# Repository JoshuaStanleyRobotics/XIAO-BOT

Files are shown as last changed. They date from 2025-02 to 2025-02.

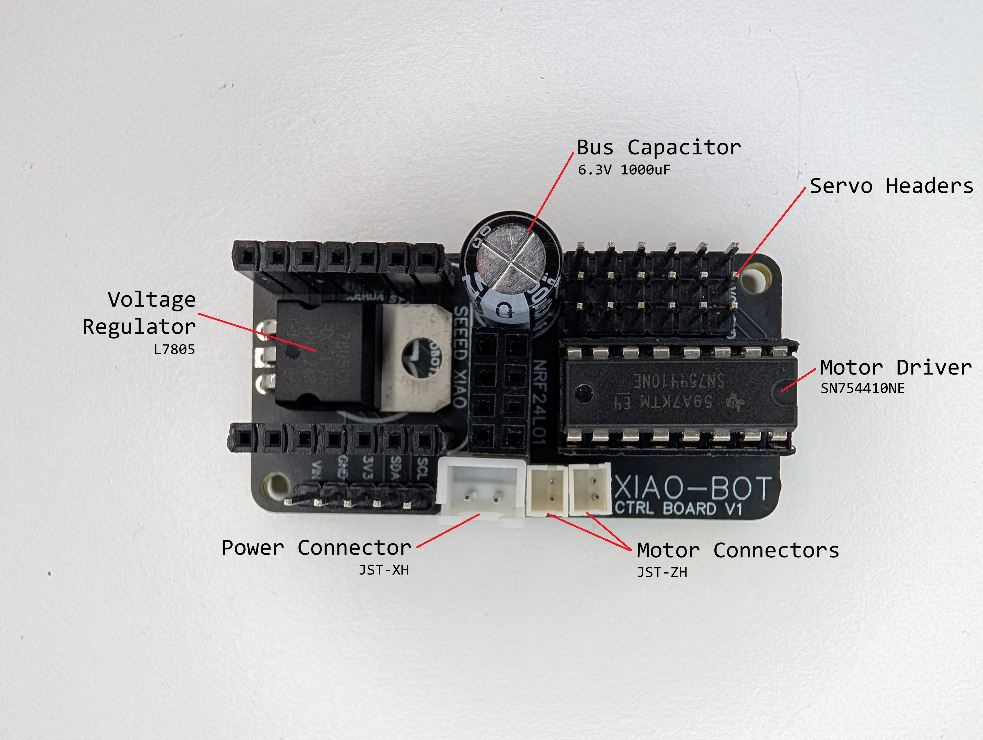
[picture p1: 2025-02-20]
Control Board/Images/04_Optional Components.jpg

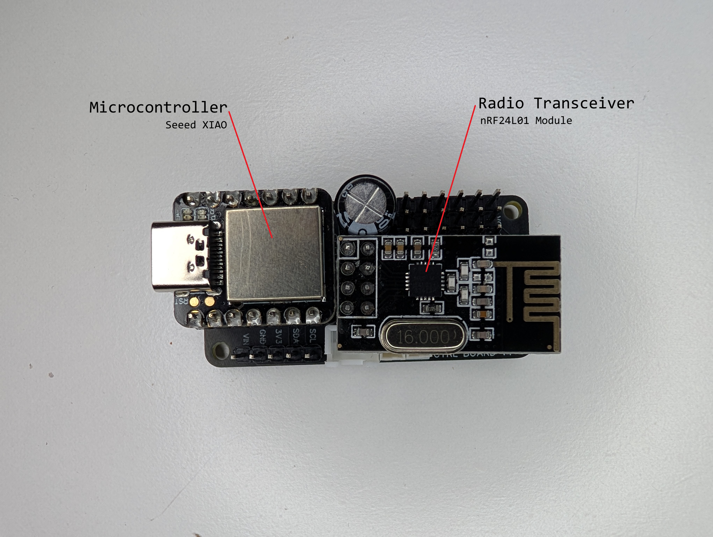
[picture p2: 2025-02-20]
Control Board/Images/03_Required Components.jpg

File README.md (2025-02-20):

# XIAO-BOT

## Control Board


The Control Board interfaces the microcontroller (a Seeed XIAO board) with a radio transceiver (nRF24L01 module) to act as the base of a compact, remote control robotics platform.
  The nRF24L01 board is wired to the standard SPI pins on the XIAO with the CE and CSN pins wired to D6 and D7 respectively. For a compatible remote check out https://github.com/JoshuaStanleyRobotics/Robot-Remote
	
Breakout servo headers are included wired to pins D0-D5 to allow for controlling up to 6 servo motors at once. 
	On the bottom side of the board, there are solder pads to select the supply voltage (VCC) for the servo headers and motor driver.
		Solder the corresponding pad to the center pad to select either the voltage supplied to the board (VIN) or the regulated voltage (5V).
	Space for an optional bus capacitor is included to help smooth the 5V supply voltage. 

A second set of breakout pins include power and I2C connections for expansions boards.
  Note: I2C uses pins D4 and D5 so these will not be usable through the servo header while an I2C device is in use.

An optional double H-bridge driver chip is included for driving up to two brushed DC motors. 
  The direction pins for motor 1 are wired to pins D0 and D1 with the enable pin wired to pin D4. 
  The direction pins for motor 2 are wired to pins D2 and D3 with the enable pin wired to pin D5.

An optional voltage regulator (L7805) can be used if the supply voltage is outside of the microcontrollers input voltage range (> 7 volts).
  To bypass this voltage regulator, solder all three voltage select solder pads together on the underside of the board. 
  This will directly connect the input power to the 5V pin on the microcontroller.

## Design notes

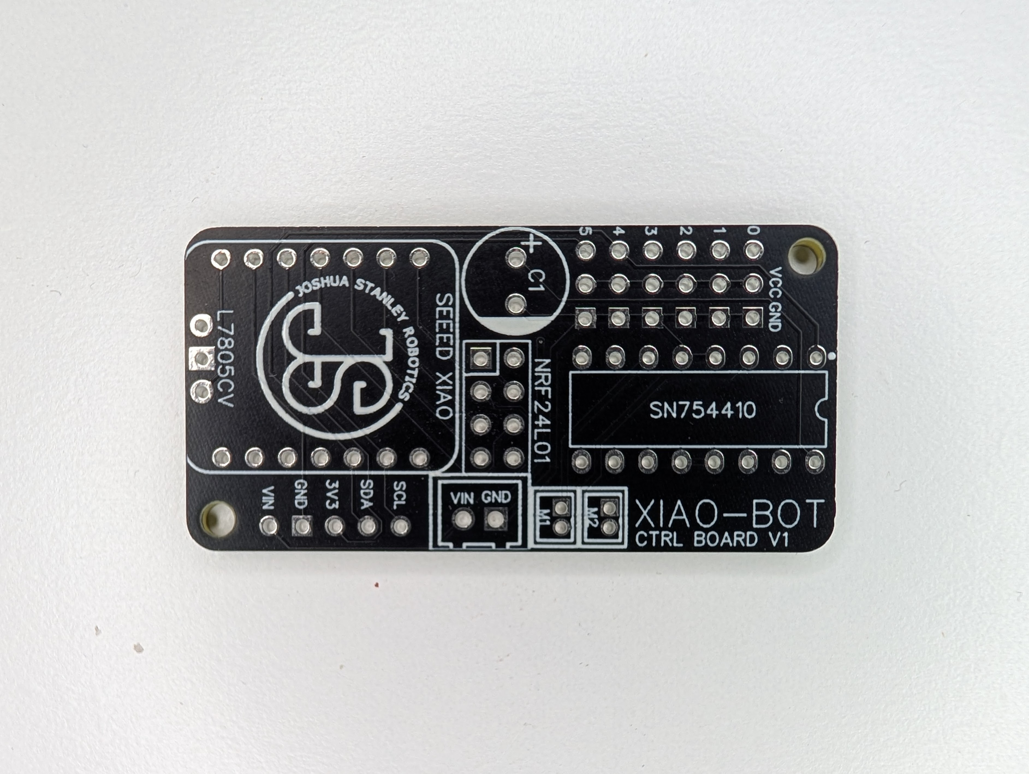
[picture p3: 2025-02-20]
Control Board/Images/01_Top View.jpg

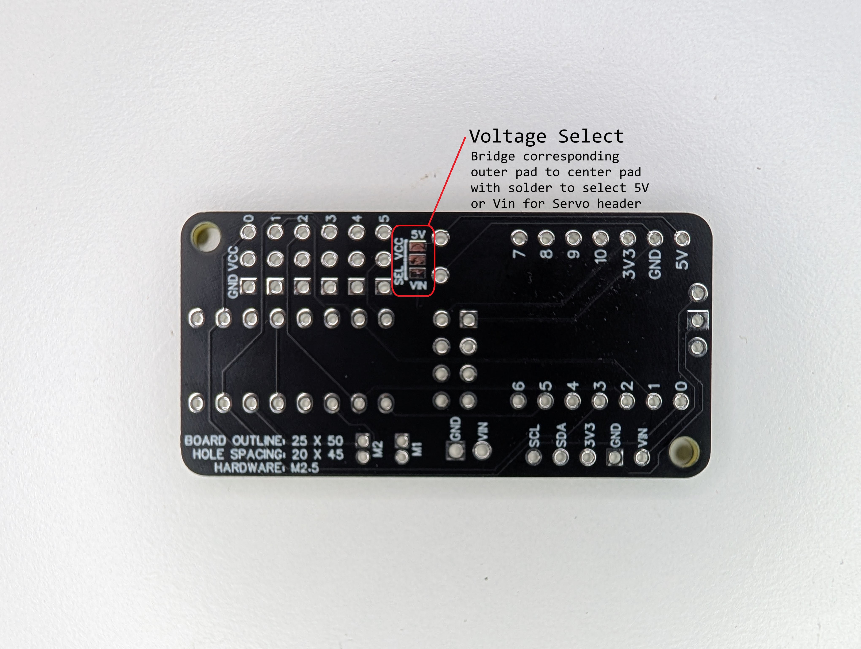
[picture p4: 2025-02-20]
Control Board/Images/02_Bottom View.jpg

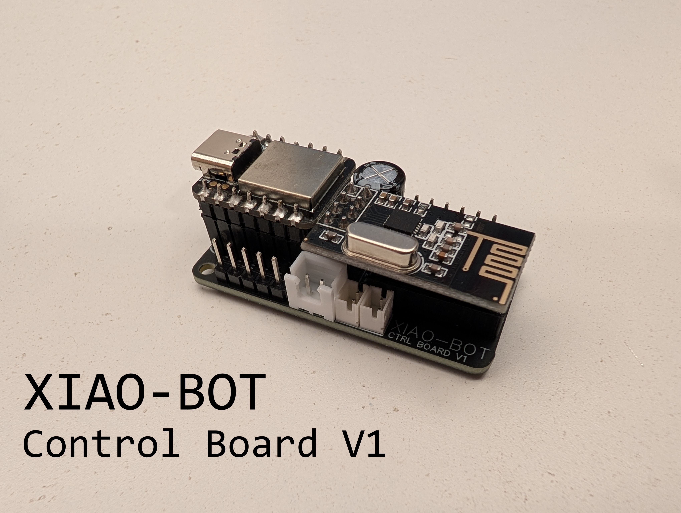
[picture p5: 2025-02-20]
Control Board/Images/05_Completed.jpg

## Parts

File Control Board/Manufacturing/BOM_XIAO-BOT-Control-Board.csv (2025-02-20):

ID | Name | Designator | Footprint | Quantity | Manufacturer Part | Manufacturer | Supplier | Supplier Part | Price
1 | 1000uF | C1 | CAP-TH_BD8.0-P3.50-D0.6-FD-2 | 1 | 6.3YXJ1000M8X11.5 | rubycon(红宝石) | LCSC | C694350 | 0.121
2 | HDR_2.54_1x5 | H1 | HDR_2.54_1X5 | 1
3 | D0-5 | H3 | HDR_2.54_3X6 | 1
4 | 1.5 JST | M1,M2 | CONN-TH_2P-P1.50_JST_B2B-ZR-K | 2 | B2B-ZR-K(LF)(SN) | JST | LCSC | C565960 | 0.078
5 | XHB-2A Connector | PWR | CONN-TH_XHB-2A | 1 | XHB-2A | BOOMELE(博穆精密) | LCSC | C57981 | 0.01
6 | NRF24L01 | U2 | HDR-F-2.54_2X4 | 1 |  |  | LCSC | C239344 | 0.165
7 | SN754410 | U3 | PDIP-16_L19.3-W6.4-P2.54-LS7.94-BL | 1 | 74F253PC | onsemi(安森美) | LCSC | C3231508 | 0.155
8 | L7805CV | U4 | L7805 | 1

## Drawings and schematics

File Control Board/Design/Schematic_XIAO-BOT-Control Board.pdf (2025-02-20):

Power | Headers

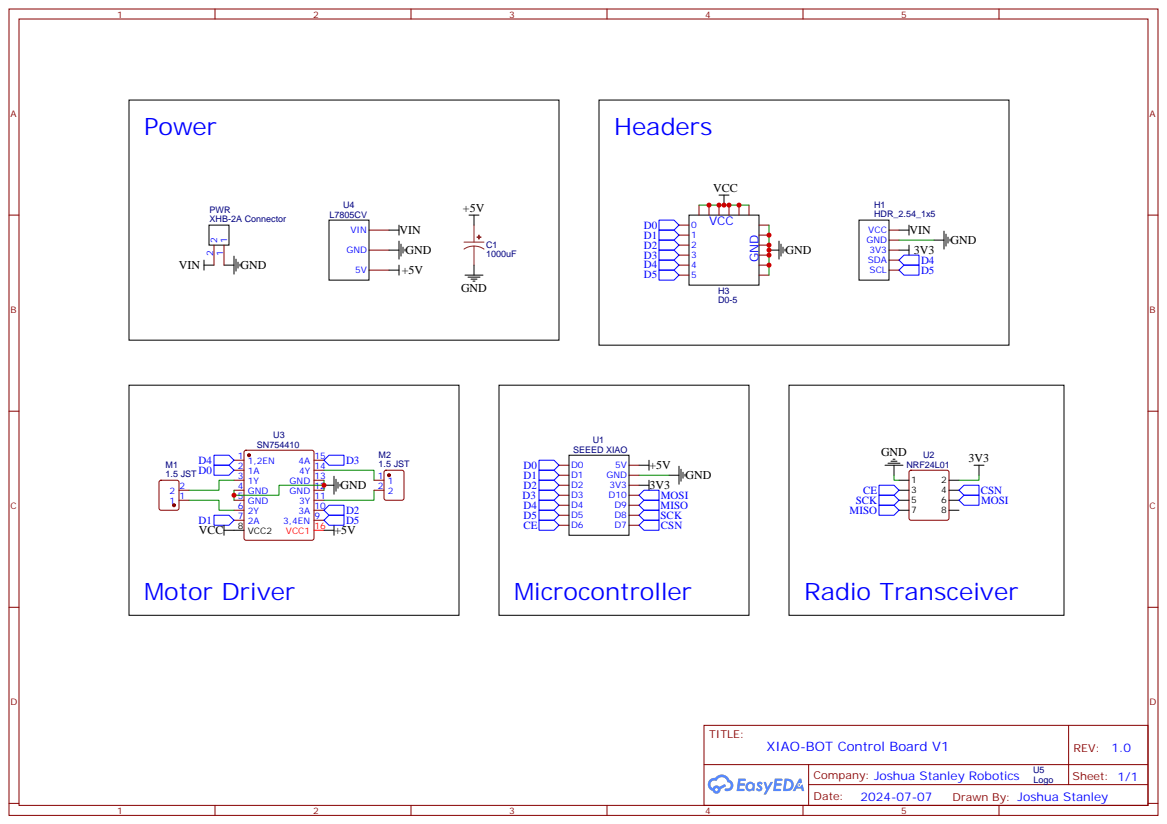
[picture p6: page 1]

Drawn By: Joshua Stanley

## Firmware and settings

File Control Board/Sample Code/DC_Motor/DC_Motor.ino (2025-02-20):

const int M1A = 0;
const int M1B = 1;
const int M2A = 2; 
const int M2B = 3;
const int M1En = 4; 
const int M2En = 5; 

void setup() {
  Serial.begin(9600);                         //Begin serial communication
  Serial.println("Serial Communication Initialized");

  pinMode(M1A, OUTPUT);
  pinMode(M1B, OUTPUT);
  pinMode(M2A, OUTPUT);
  pinMode(M2B, OUTPUT);
  pinMode(M1En, OUTPUT);
  pinMode(M2En, OUTPUT);
  digitalWrite(M1En, HIGH);
  digitalWrite(M2En, HIGH);
  Serial.println("Motors Set");
}

void loop() {
  digitalWrite(M1A, HIGH);                    //Full speed forward
  digitalWrite(M1B, LOW);
  digitalWrite(M2A, HIGH);
  digitalWrite(M2B, LOW);
  analogWrite(M1En, 255);
  analogWrite(M2En, 255);
  delay(1000);

  digitalWrite(M1A, LOW);                     //Half speed backwards
  digitalWrite(M1B, HIGH);
  digitalWrite(M2A, LOW);
  digitalWrite(M2B, HIGH);
  analogWrite(M1En, 123);
  analogWrite(M2En, 123);
  delay(1000);

  digitalWrite(M1A, LOW);                     //Off
  digitalWrite(M1B, LOW);
  digitalWrite(M2A, LOW);
  digitalWrite(M2B, LOW);
  analogWrite(M1En, 0);
  analogWrite(M2En, 0);
  delay(1000);
}

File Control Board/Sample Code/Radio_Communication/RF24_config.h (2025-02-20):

/*
 Copyright (C)
    2011            J. Coliz <maniacbug@ymail.com>
    2015-2019       TMRh20
    2015            spaniakos <spaniakos@gmail.com>
    2015            nerdralph
    2015            zador-blood-stained
    2016            akatran
    2017-2019       Avamander <avamander@gmail.com>
    2019            IkpeohaGodson
    2021            2bndy5

 This program is free software; you can redistribute it and/or
 modify it under the terms of the GNU General Public License
 version 2 as published by the Free Software Foundation.
*/

#ifndef __RF24_CONFIG_H__
#define __RF24_CONFIG_H__

/*** USER DEFINES:    ***/
#define FAILURE_HANDLING
//#define SERIAL_DEBUG
//#define MINIMAL
//#define SPI_UART    // Requires library from https://github.com/TMRh20/Sketches/tree/master/SPI_UART
//#define SOFTSPI     // Requires library from https://github.com/greiman/DigitalIO

/**
 * User access to internally used delay time (in microseconds) during RF24::powerUp()
 * @warning This default value compensates for all supported hardware. Only adjust this if you
 * know your radio's hardware is, in fact, genuine and reliable.
 */
#if !defined(RF24_POWERUP_DELAY)
#define RF24_POWERUP_DELAY	5000
#endif

/**********************/
#define rf24_max(a, b) (a>b?a:b)
#define rf24_min(a, b) (a<b?a:b)

/** @brief The default SPI speed (in Hz) */
#ifndef RF24_SPI_SPEED
#define RF24_SPI_SPEED 10000000
#endif

//ATXMega
#if defined (__AVR_ATxmega64D3__) || defined (__AVR_ATxmega128D3__) || defined (__AVR_ATxmega192D3__) || defined (__AVR_ATxmega256D3__) || defined (__AVR_ATxmega384D3__)
// In order to be available both in Windows and Linux this should take presence here.
    #define XMEGA
    #define XMEGA_D3
    #include "utility/ATXMegaD3/RF24_arch_config.h"

// RaspberryPi rp2xxx-based devices (e.g. RPi Pico board)
#elif defined (PICO_BUILD) && !defined (ARDUINO)
    #include "utility/rp2/RF24_arch_config.h"

#elif (!defined (ARDUINO)) // Any non-arduino device is handled via configure/Makefile
    // The configure script detects device and copies the correct includes.h file to /utility/includes.h
    // This behavior can be overridden by calling configure with respective parameters
    // The includes.h file defines either RF24_RPi, MRAA, LITTLEWIRE or RF24_SPIDEV and includes the correct RF24_arch_config.h file
    #include "utility/includes.h"

//ATTiny
#elif defined (__AVR_ATtiny25__) || defined (__AVR_ATtiny45__) || defined (__AVR_ATtiny85__) || defined (__AVR_ATtiny24__) || defined (__AVR_ATtiny44__) || defined (__AVR_ATtiny84__) || defined (__AVR_ATtiny2313__) || defined (__AVR_ATtiny4313__) || defined (__AVR_ATtiny861__) || defined (__AVR_ATtinyX5__) || defined (__AVR_ATtinyX4__) || defined (__AVR_ATtinyX313__) || defined (__AVR_ATtinyX61__)
    #define RF24_TINY
    #include "utility/ATTiny/RF24_arch_config.h"

#elif defined (LITTLEWIRE) //LittleWire
    #include "utility/LittleWire/RF24_arch_config.h"

#elif defined (TEENSYDUINO) //Teensy
    #include "utility/Teensy/RF24_arch_config.h"

#else //Everything else
    #include <Arduino.h>


    #if defined (ARDUINO) && !defined (__arm__) && !defined (__ARDUINO_X86__)
        #if defined SPI_UART
            #include <SPI_UART.h>
            #define _SPI uspi
        #elif defined (SOFTSPI)
            // change these pins to your liking
            //
            #ifndef SOFT_SPI_MISO_PIN
                #define SOFT_SPI_MISO_PIN 9
            #endif // SOFT_SPI_MISO_PIN

            #ifndef SOFT_SPI_MOSI_PIN
                #define SOFT_SPI_MOSI_PIN 8
            #endif // SOFT_SPI_MOSI_PIN

            #ifndef SOFT_SPI_SCK_PIN
                #define SOFT_SPI_SCK_PIN 7
            #endif // SOFT_SPI_SCK_PIN

            const uint8_t SPI_MODE = 0;
            #define _SPI spi

        #elif defined (ARDUINO_SAM_DUE)
            #include <SPI.h>
            #define _SPI SPI

        #else // !defined (SPI_UART) && !defined (SOFTSPI)
            #include <SPI.h>
            #define _SPI SPIClass
            #define RF24_SPI_PTR
        #endif // !defined (SPI_UART) && !defined (SOFTSPI)

    #else // !defined(ARDUINO) || defined (__arm__) || defined (__ARDUINO_X86__)
        // Define _BV for non-Arduino platforms and for Arduino DUE
        #include <stdint.h>
        #include <stdio.h>
        #include <string.h>

        #if defined (__arm__) || defined (__ARDUINO_X86__)
            #if defined (__arm__) && defined (SPI_UART)
                #include <SPI_UART.h>
                #define _SPI uspi

            #else // !defined (__arm__) || !defined (SPI_UART)
                #include <SPI.h>
                #define _SPI SPIClass
                #define RF24_SPI_PTR
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
